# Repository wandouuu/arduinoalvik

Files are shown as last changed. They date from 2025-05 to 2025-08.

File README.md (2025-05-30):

# Autonomy in Action with the Arduino Alvik
Repository of the code used to develop a line following robot with color recognition. Developed by Semih Eski and Brendan Leung, students at Dawson College during the Winter 2025 Semester.
# About This Project
This is an open-source autonomous vehicle project that uses an Arduino Alvik. It extends beyond Alvik's out-of-box capabilities by bringing together a Raspberry Pi 3B+, used for computer vision, and a 3D-printed 5-DOF robotic arm. Alvik leverages a PID algorithm and its infrared sensors to do line following, and its color-recognition sensor to detect colors underneath. A Raspberry Pi and a Pi camera are mounted on a 3D-printed stable makeshift holder that is secured through Alvik's screw threads. When the Alvik detects the color white underneath, it stops and commands, through serial communication, the RPi to run a computer vision program to calculate the distance from Alvik to a ping pong ball placed ahead. The RPi returns the distance to Alvik who accurately calculates time to travel at a fixed RPM, drives and stops next to the ball. The RPi then controls the robotic arm to pick up the ball through the PCA9685 servo board using inverse kinematics. Alvik continues travelling around the track until it detects the color orange, placed next to a basket, in which the robotic arm drops the ping pong ball. Alvik continues moving around the track until it is stopped.
# Features
* PID line following
* HSV color detection
* Touch sensor
* Serial communication
* Computer vision color recognition
* Computer vision distance calculation
* Inverse kinematics
# Hardware Requirements
* Arduino Alvik
* Raspberry Pi 3B+
* 3D printed robotic arm
* PCA9685 servo board
* Raspberry Pi camera module 1
* Jumper wires
* Black electrical tape
* 8xM3x15mm screws
* 6xFS90 micro servos
* 5V/2.5A+ portable power supply
* 5V/5A USB battery pack
# Files
* `serialcomm.py`: Main RPi sketch for serial communication, computer ball recognition and vision distance calculation
* `snap_photo.py`: Captures a photo through the RPi camera
* `distancecalc.py`: RPi sketch for only calculating distance
* `ball_color_detection.py`: RPi sketch for only ball detectiong and drawing a contour
* `line_follower.ino`: Main Arduino sketch for line following, HSV color recognition and serial communication
* `robot_arm_parts`: All the parts to 3D print in .SLDPRT format
# Getting Started
## Wiring Instructions
### Raspberry Pi → Alvik's Nano ESP32: 
* USB-A → USB Micro B
### Raspberry Pi → PCA9685:
* 3.3V → VCC
* SDA → SDA
* SCL → SCL
* GND → GND
### Servos → PCA9685:
* Servo 1 → PCA9685 Pin 0
* Servo 2 → PCA9685 Pin 1
* Servo 3 → PCA9685 Pin 2
* Servo 4 → PCA9685 Pin 3
* Servo 5 → PCA9685 Pin 4
* Servo 6 → PCA9685 Pin 5
## Prerequisites
* Python
* Arduino IDE
* Arduino Alvik Library (should be installed by default)
* Thonny IDE (Raspberry Pi)
* OpenCV (Raspberry Pi)
* NumPy (Raspberry Pi)
* imutils (Raspberry Pi)
## Cloning the repository
```bash
# Navigate on your computer to a directory (folder) in which you contain your repositories
cd directory1/directory2/directory3/.../my_repos

# In your my_repos directory, or whatever your folder name may be, clone our GitHub repository by doing the following
git clone https://github.com/wandouuu/arduinoalvik.git

# Now, you should be in the my_repos folder. From there, go into the arduinoalvik directory to access the content
cd arduinoalvik

# Before installing any dependencies for the Raspberry Pi, ensure that the apt-get function is fully updated
sudo apt-get update

# And install any prerequisites
sudo apt-get install build-essential cmake pkg-config libjpeg-dev libtiff5-dev libjasper-dev libpng-dev libavcodec-dev libavformat-dev libswscale-dev libv4l-dev libxvidcore-dev libx264-dev libfontconfig1-dev libcairo2-dev libgdk-pixbuf2.0-dev libpango1.0-dev libgtk2.0-dev libgtk-3-dev libatlas-base-dev gfortran libhdf5-dev libhdf5-serial-dev libhdf5-103 python3-pyqt5 python3-dev -y

```
## Keeping apt-get updated on the Raspberry Pi
```bash
# Before installing any dependencies for the Raspberry Pi, ensure that the apt-get function is fully updated by writing the following into Raspberry Pi's terminal
sudo apt-get update

# And install any prerequisites
sudo apt-get install build-essential cmake pkg-config libjpeg-dev libtiff5-dev libjasper-dev libpng-dev libavcodec-dev libavformat-dev libswscale-dev libv4l-dev libxvidcore-dev libx264-dev libfontconfig1-dev libcairo2-dev libgdk-pixbuf2.0-dev libpango1.0-dev libgtk2.0-dev libgtk-3-dev libatlas-base-dev gfortran libhdf5-dev libhdf5-serial-dev libhdf5-103 python3-pyqt5 python3-dev -y
```
## OpenCV Installation
```bash
# Still in the Raspberry Pi terminal, type:
pip install opencv-python==4.5.3.56
```

## NumPy Installation
```bash
# Still in the Raspberry Pi terminal, type:
pip install numpy
```

## imutils Installation
```bash
# Still in the Raspberry Pi terminal, type:
pip install imutils
```
Hooray, you have installed now installed the necessary dependencies! You may now get to work!

# How to Use
1. Make a simple, circular track with a white gap at the beginning of a straight segment of track.
2. Attach the wires as indicated in the Wiring Instructions. Note that the camera should be facing the front of the Alvik.
3. Ensure that the Alvik is sufficiently charged.
4. Ensure that the Raspberry Pi is plugged into an outlet or a portable power supply with adequate voltage and amperage.
5. Find the RGB values of the white line, read through Alvik's color-recognition sensor, where the Alvik will stop on the line following track and input them in the `line_follower.ino` if statement with the comparison operators with the rgb_colors list.
6. Upload `serialcomm.py` to the Arduino Alvik using the Arduino IDE.
7. Using `ball_color_detection.py`, ensure that the coloured ping pong ball is detected in your given lighting conditions. Adjust the parameters ORANGE_LOWER and ORANGE_UPPER as needed to detect the ping pong ball.
8. Copy and paste these values across to serialcomm.py.
9. Now, write the directory in `snap_photo.py` of where the calibration photo is stored. 
10. Run the program `snap_photo.py` and disconnect the HDMI cable (ensure the Alvik and the Pi are connected via USB) and run the Alvik by turning it on and pressing the checkmark on the top of it.
11. Once the photo is taken, ensure the calibration photo directory (calib_path variable) is the same as in `serialcomm.py`. 
12. In `serialcomm.py`, write the directory in which the photo of the distance calculation photo will be taken in the capture method of the camera object.
13. Run `serialcomm.py` and detach the HDMI cable, ensuring the Alvik and the Pi are connected via USB.
14. Turn on Alvik and press its checkmark and watch it go!

# Development Notes
- Created as part of the MakerSPACE initiative and Making Things That Matter course at Dawson College.
- Version 1.0.0

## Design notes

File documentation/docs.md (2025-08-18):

# Arduino Alvik: Developing a Project in Engineering Robotics from Scratch!
## Project developed by Semih Eski and Brendan Leung, Report written by Brendan Leung
### Introduction
<p>&nbsp;&nbsp;&nbsp;&nbsp;Independent learning is something that we have struggled with. How do we build a project from scratch? How do we acquire the skills we need to conceive a project we are interested in? Along with our continued interest for computers, programming, computer and mechanical engineering we aimed to learn the art of learning by exploring engineering robotics as beginners and documenting our journey so that future beginners can see how we modeled a path to learning how to develop a project from nothing. We wished to be able to learn on the fly, adapt and conceive a project that involves hardware and software from start to finish. With our project, we were able to get hands-on with robots and software to realize this goal and gain the experience and technical skills we need to create a project from nothing.</p>
<p>&nbsp;&nbsp;&nbsp;&nbsp;Our goal was achieved using the Arduino Alvik robot, a premade robot made by Arduino, an open-source hardware company known for their electronics. Together with this robot, we built a robot capable of picking up coloured ping pong balls from a line following track using a Raspberry Pi, a Linux-based computer used in various electronics projects, to identify the colours of the ping pong balls using a camera. We also designed a custom-made robotic arm for the Alvik, which was integrated with its hardware to help pick up the balls off the ground. </p>

### Project Description
<ul>
<li><b>Objective</b></li>
<p>&nbsp;&nbsp;&nbsp;&nbsp; The goal of our project was to discover a learning path for engineering robotics. We focused on acquiring the experience we needed to develop a project in a field we had and still have a fond interest in, as well as the necessary skills we need to use software and hardware to develop a project. </p>
<li><b>Inspiration</b></li>
<p>&nbsp;&nbsp;&nbsp;&nbsp; When we were young, we became fondly interested in electronics and mechanical devices, but we never knew where to start. We were fascinated at how people were able to make these cool gadgets, but we struggled to put our hands on it. We struggled to program. We struggled to build. But we never struggled to dream that I could program and build things on my own. We knew we had to start somewhere. We knew we had to learn by doing something. So, we chose to design a project with the Arduino Alvik robot, a premade robot conceived by Arduino, an open-source hardware company known for their microcontrollers and other electronics. </p>
<p>&nbsp;&nbsp;&nbsp;&nbsp; While we could have built a robot from scratch, we decided to use the Alvik because it helped us gain a solid foundation for how hardware and software interact with each other without having to think about wiring and connections. For example, we learned along the way that the communication between hardware and software has to be exact. We realized that the way I think the robot would behave with the code we implemented sometimes did not work out in practice. Additionally, we wished to extend the already existing capabilities of the Alvik and learn how different technologies could be implemented with each other. Needless to say, we were ambitious. We used a Raspberry Pi, a Linux-based computer, to help with serial communication between a robotic arm from scratch and the Alvik, so that the Alvik is able to recognize coloured ping pong balls and pick them off the ground using its robotic arm. </p>
<p>&nbsp;&nbsp;&nbsp;&nbsp;Our inspiration largely came from experimenting at the beginning of our project with the robot with my teammate and the project was better understood after learning what we were both capable of.</p>
<li><b>Design and Planning</b></li>
<p>&nbsp;&nbsp;&nbsp;&nbsp; At the beginning of my project, we were not fully sure what to do. We wanted to develop a project using artificial intelligence to make the Alvik drive around autonomously, but soon enough this turned out unfeasible in the time we had. However, we were determined to keep the essence of that idea inside of our project. After much brainstorming, we made our idea much more feasible, incorporating line following features to imitate this autonomous navigation. As described in our journals early on, we began first exploring different functionalities of the robot. Figure 1 below shows us playing around with the robot, attempting to make the Alvik find the object it is closest to.</p>
<figure>
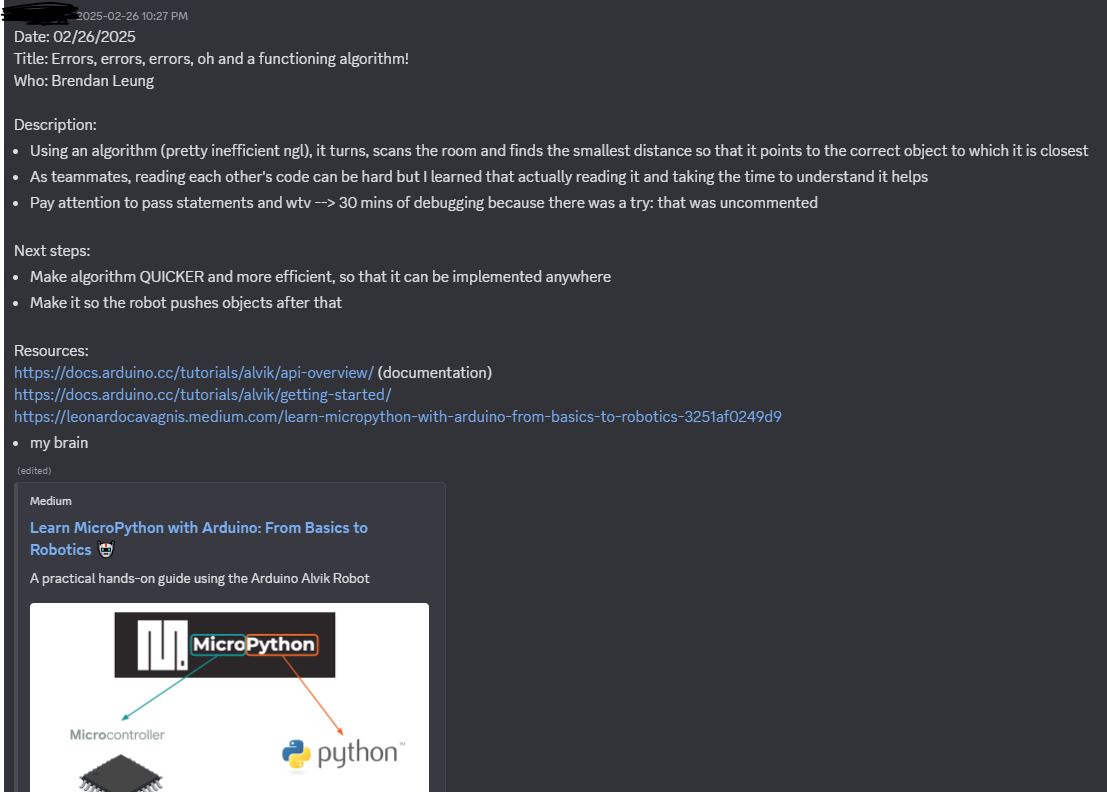
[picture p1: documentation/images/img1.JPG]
Experimenting with Alvik for the First Time!
    
    <figcaption><em>Figure 1. Our history of what we did was written in Discord. In a journal three months ago, we tried making the robot point towards the object it was closest to. It seems like it was successful, but it was quite slow!</em></figcaption>
</figure>
<p>&nbsp;&nbsp;&nbsp;&nbsp;These days helped both of us become familiar with the robot and its capabilities. At the time, we thought of making a robot that could push objects off the table; of course, without making the Alvik fall off the table itself! Because our program was quite straightforward, we wanted to make something more elaborate. </p>
<p>&nbsp;&nbsp;&nbsp;&nbsp;We interviewed a Masters student from the University of Toronto specializing in robotics and AI to help guide us in our project. Our ambition was soon met with realistic expectations, as she told us that AI would be quite difficult and we should only implement it if we had time. Then, she told us that we should divide our project into little chunks, tackling each small problem progressively and combining them together later. This strategy helped me in the project development because, as beginners, we were quite overwhelmed with the amount of features we had to consider. Instead, breaking the project up into smaller, more manageable pieces made the project seem more achievable. This is how we tackled different parts of the project. </p>
<p>&nbsp;&nbsp;&nbsp;&nbsp;This idea had major implications on how we worked on our project because we knew we had a learning path. We had a roadmap. We knew we wanted to make a robot capable of driving itself around and have some image recognition capabilities. With that, in the months following, we focused on developing Alvik’s functions: line following, object detection, colour detection and etc. Semih also focused on creating the robotic arm and integrating it with our robot. Below is a snapshot of the prototype of the Alvik along with its robotic arm.<p>
<figure>
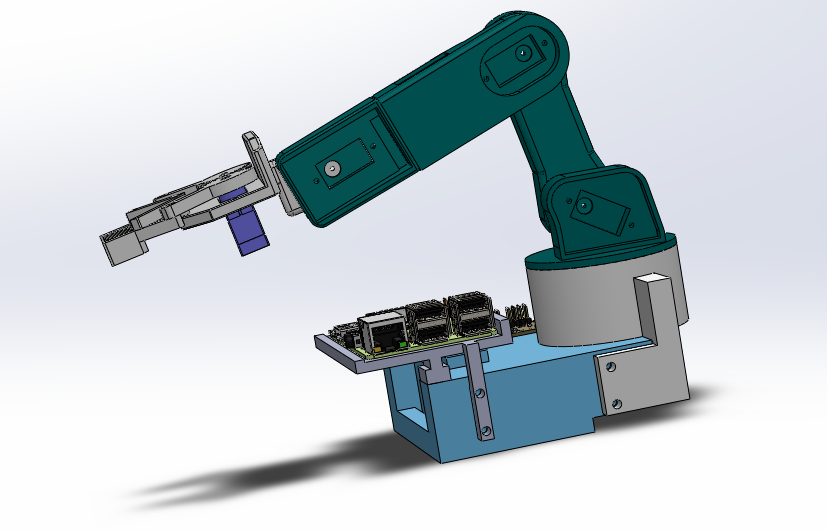
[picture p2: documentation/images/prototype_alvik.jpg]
Prototype of Alvik and its Robotic Arm
  
  <figcaption><em>Figure 2. The Alvik is shown with a Raspberry Pi holder near the front of the Alvik while a robotic arm sits as a counterbalance towards the back of the Alvik.</em></figcaption>
</figure>
<p>&nbsp;&nbsp;&nbsp;&nbsp; In our final stage, we implemented all these smaller chunks together in what will be a robot which is capable of line following and picking up coloured ping pong balls in its vicinity.</p>
</ul>

### Implementation
<ul>
<li><b>Hardware Setup</b></li>
<ul>
<li>Components Used</li>
<ul>
<li>Arduino Alvik</li>
<li>Raspberry Pi 3 Model B+</li>
<li>Raspberry Pi Camera Module 1</li>
<li>3D Printed Robotic Arm</li>
<li>Six SG90 Positional Servos</li>
<li>PCA9685 Servo Driver</li>
<li>Power Supplies</li>
</ul>
<li>Hardware Schematics</li>
<p>&nbsp;&nbsp;&nbsp;&nbsp; The serial connection between the Arduino Alvik and the Raspberry Pi is made via Universal Serial Bus (USB). The Alvik should be connected to the Raspberry Pi using its USB-C port, connected to the designated USB-A port on the Raspberry Pi, as shown in the diagram below. Note that if a different port is chosen, the USB port chosen to establish serial communication in the Python code will have to be changed.</p>

<figure>
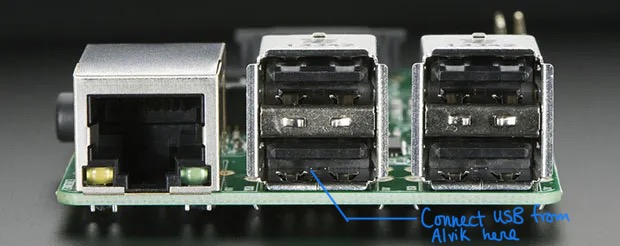
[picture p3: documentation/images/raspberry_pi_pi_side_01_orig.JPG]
Side image of the USB-A connection on the Raspberry Pi
    
    <figcaption><em>Figure 3. Connect the Alvik to the Raspberry Pi in the exact port on the Raspberry Pi as shown. The other end should be connected to the USB-C port of the Alvik.</em></figcaption>
</figure>

<p>&nbsp;&nbsp;&nbsp;&nbsp; To connect the servos, connect the female-to-female jumper wires between the Raspberry Pi and the Servo Driver as follows. Also, attach the Raspberry Pi Camera Module in the slot that is named "Camera". This is shown in the figure below:</p>
<figure>
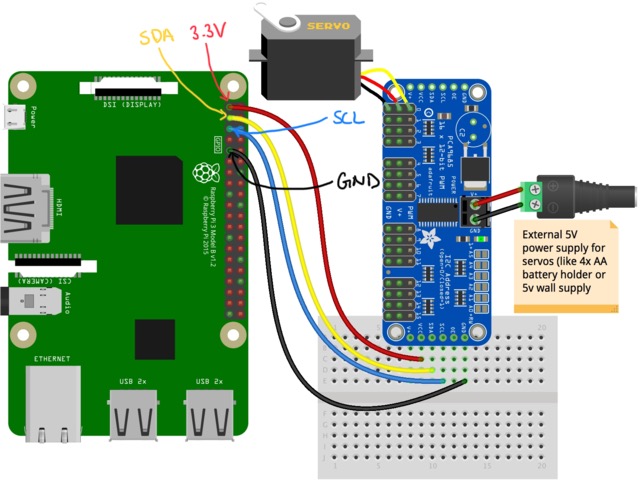
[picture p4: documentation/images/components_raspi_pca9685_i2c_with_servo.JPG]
Connections on the Raspberry Pi and between it and the Servo Drivers
    
    <figcaption><em>Figure 4. Connect the female-to-female wires as shown between the Raspberry Pi and the Servo Driver. Furthermore, connect the Raspberry Pi Camera Module in the "Camera" slot.</em></figcaption>
</figure>
<p>&nbsp;&nbsp;&nbsp;&nbsp; Note that to read any information that is serially monitored by the Alvik or the Raspberry Pi, the Raspberry Pi (not the Alvik) must be connected to a monitor via HDMI. This is because the Alvik sends all its serial information to the Raspberry Pi, and the Raspberry Pi can display this information along with its own. Finally, the Raspberry Pi must be plugged into an outlet, while the Alvik can be charged. Ensure as well that the wiring has enough slack to allow for the Alvik to be mobile.</p>
</ul>

<li><b>Software Development</b></li>
<ul>
<li>Libraries Used</li>
<ul>
<li>Arduino Alvik Library</li>
<li>Serial Library</li>
<li>OpenCV</li>
<li>OS</li>
<li>NumPy</li>
<li>imutils</li>
</ul>
</ul>
<p>&nbsp;&nbsp;&nbsp;&nbsp; The code specific to the Alvik was developed using the Arduino IDE, while the code for the Raspberry Pi was written on the Pi's text editor. All of Alvik's functions can be found on <a href = "https://docs.arduino.cc/tutorials/alvik/api-overview/">Alvik's API</a>, which provides all the details of each method. It is important to note that while Arduino claims that all functions work between MicroPython and C++, we encountered runtime errors where the C++ compiler was unable to locate a function like alvik.drive(). We used Alvik's API extensively in our project, making this a valuable site for learning how to make the Alvik move, how to use its sensors, etc. We also used Arduino's own courses, found <a href = "https://www.arduino.cc/education/courses">here</a>, which helped us learn early on how to make Alvik follow a line and detect objects in front of it. It is a fantastic way to familiarize yourself with all that Alvik offers out-of-the-box before trying out more ambitious ideas. </p>
<p>&nbsp;&nbsp;&nbsp;&nbsp; To detect the ping pong balls, we used OpenCV, a library used for real-time computer vision, which runs locally on the Raspberry Pi and then sends the information back to the Alvik using serial communication. The code below, inspired by <a href="https://github.com/freedomwebtech/colortracking/blob/main/test.py">this GitHub repository</a>, allows us to identify orange coloured ping pong balls. We initially wished to deploy a machine learning model to identify our ping pong balls; however, it was hard to deploy because of compatibility issues between Windows and Raspberry Pi. So, we elected to detect colours instead because it was compatible and, more importantly, lightweight to run on the Raspberry Pi. Still, OpenCV provides us with a powerful computer vision library that suits our needs. NumPy was used extensively to store HSV values, while OS provided us with an easier way to manage file directories.</p>

```py
# Import OpenCV and NumPy Libraries
import cv2
import numpy as np

# Initialize camera
cap = cv2.VideoCapture(0)
cap.set(cv2.CAP_PROP_FRAME_WIDTH,  640)
cap.set(cv2.CAP_PROP_FRAME_HEIGHT, 480)

# Upper and Lower Bounds for the color to be identified (in HSV NOT RGB)
ORANGE_LOWER = np.array([ 6, 120, 160]) # Set these values depending on your specific lighting conditions and what color you would like to identify
ORANGE_UPPER = np.array([26, 255, 255])

kernel = np.ones((5, 5), np.uint8)   # this is used for morphology

while True:
    success, frame = cap.read()

    # If fails to read camera data
    if not success:
        print("Camera read failed — exiting.")
        break

    # Color spectrum used
    hsv = cv2.cvtColor(frame, cv2.COLOR_BGR2HSV)

    # Color mask
    orange_mask = cv2.inRange(hsv, ORANGE_LOWER, ORANGE_UPPER)
    mask = orange_mask

    mask = cv2.morphologyEx(mask, cv2.MORPH_OPEN,  kernel, iterations=1)
    mask = cv2.morphologyEx(mask, cv2.MORPH_CLOSE, kernel, iterations=1)

    contours, _ = cv2.findContours(mask, cv2.RETR_EXTERNAL, cv2.CHAIN_APPROX_SIMPLE)
    
    # If it detects an orange mask
    if contours:
        c = max(contours, key=cv2.contourArea)
        if cv2.contourArea(c) > 300:        # Ensures that tiny specs are not identified
            
            # Locates the position of the color to be identified
            (x, y), radius = cv2.minEnclosingCircle(c)
            centre = (int(x), int(y)); radius = int(radius)

            cv2.circle(frame, centre, radius, (0, 255,   0), 2)
            cv2.circle(frame, centre,   3,    (0,   0, 255), -1)
            cv2.putText(frame, "orange ball",
                        (centre[0] - 40, centre[1] - radius - 10),
                        cv2.FONT_HERSHEY_SIMPLEX, 0.6, (255, 255, 255), 2)

    cv2.imshow("Mask (debug)", mask)
    cv2.imshow("Ball contour", frame)

    if cv2.waitKey(1) & 0xFF == ord('q'):
        break

cap.release()
cv2.destroyAllWindows()
```
<p>&nbsp;&nbsp;&nbsp;&nbsp; The success rate of this piece of software heavily depends on the lighting conditions in which we were in. We struggled mostly to land consistent results, given that the lighting conditions in which we found ourselves when testing our software were always different. We always had to constantly tweak the lower and upper bounds for colour so that the orange ball is detected in each specific lighting conditions in which we were in. Not only did the orange ball have to be detected, but it also had to enclose the orange ball entirely and accurately pinpoint its center. This is because this was used to calculate the distance between the Alvik and the ping pong in front of it, using the code below, which was developed with the help of <a href = "https://pyimagesearch.com/2015/01/19/find-distance-camera-objectmarker-using-python-opencv/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">this website</a>. Your image should look like this: </p>

<figure>
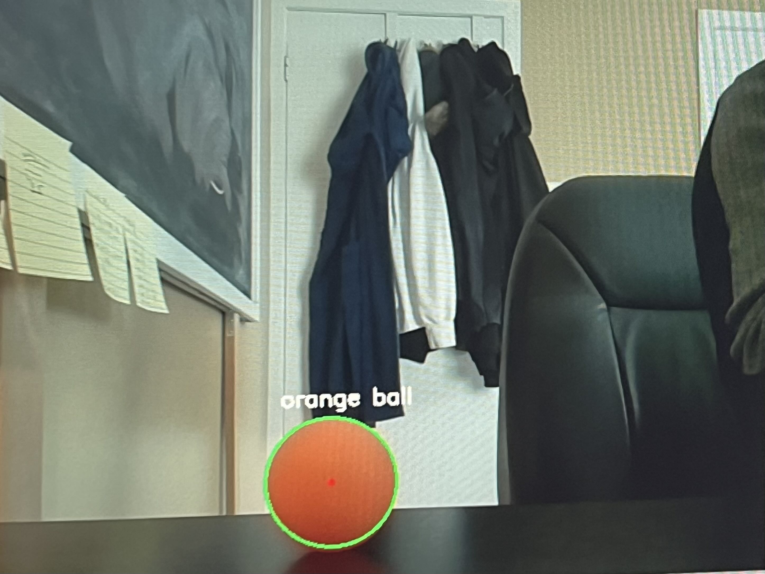
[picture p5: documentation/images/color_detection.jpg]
Orange Ping Pong Ball Perfectly Enclosed by Colour Detection Algorithm
    
    <figcaption><em>Figure 5. The colour you wish to detect should be perfectly enclosed like the photo shown above, with the red dot at the center.</em></figcaption>
</figure>

```py
# Import the necessary packages
from imutils import paths
import numpy as np
import imutils
import cv2
import os

KERNEL = np.ones((5, 5), np.uint8)       

# These bounds are exactly like the code for the ball color detection alone
ORANGE_LOWER = np.array([4,140,58])
ORANGE_UPPER = np.array([12,214,129])     

# This takes the code from the ball color detection in order to create a circle around the ping pong ball
def find_marker(image):
    hsv = cv2.cvtColor(image, cv2.COLOR_BGR2HSV)
    mask = cv2.inRange(hsv, ORANGE_LOWER, ORANGE_UPPER)

    mask = cv2.morphologyEx(mask, cv2.MORPH_OPEN, KERNEL, iterations=1)
    mask = cv2.morphologyEx(mask, cv2.MORPH_CLOSE, KERNEL, iterations=1)

    cnts = cv2.findContours(mask, cv2.RETR_EXTERNAL, cv2.CHAIN_APPROX_SIMPLE)
    cnts = imutils.grab_contours(cnts)
    if not cnts:
        return None
    c = max(cnts, key=cv2.contourArea)
    if cv2.contourArea(c) < 200:
        return None
    (x, y), radius = cv2.minEnclosingCircle(c)
    return (x, y), radius

# Calculates the distance from camera
def distance_to_camera(knownWidth_cm, focalLength_px, perWidth_px):
    return (knownWidth_cm * focalLength_px) / perWidth_px

# Below, insert the path to the photo that is required to calibrate the distance calculations
calib_path = "path of calibration photo goes here"

# Need to put the known distance of the ping pong ball from the camera from the calibration photo
KNOWN_DISTANCE_CM = 33.50 # Distance of object from camera
KNOWN_WIDTH_CM    = 4.0 # Width of object 

# Raises an error if no calibration photo exists
if not os.path.isfile(calib_path):
    raise FileNotFoundError(f"calibration image missing")

# Reads the image
calib_image = cv2.imread(calib_path)
# Before taking the photo, ensure that the camera actually detects and puts a perfect circle around the ping pong ball
res = find_marker(calib_image)
# Raises an error if the ball detection software does not detect the ball. This is why you must ensure the ball is detected prior to taking the photo.
if res is None:
    raise RuntimeError("No ball found")
(center0, radius0) = res
perWidth0 = 2 * radius0 
focalLength_px = (perWidth0 * KNOWN_DISTANCE_CM) / KNOWN_WIDTH_CM

cv2.namedWindow("image", cv2.WINDOW_NORMAL)
cv2.resizeWindow("image", 800, 600)

# Code checks for photos in a certain directory of which you have stored photos of distances of ping pong balls you wish to calculate
for imagePath in sorted(paths.list_images("path of photo goes here")): # Once there is a calibration photo, indicate where your photos are taken
    # Path of image
    image = cv2.imread(imagePath)

    # Finds ball in image
    res = find_marker(image)

    # If no ball is found, nothing is returned
    if res is None:
        dist_cm = None
    else: # Otherwise, it calculates the position and distance of the ball from the image itself
        (x, y), radius = res
        perWidth = 2 * radius
        # Calculates the distance from the camera
        dist_cm = distance_to_camera(KNOWN_WIDTH_CM, focalLength_px, perWidth)

        center = (int(x), int(y))
        cv2.circle(image, center, int(radius), (0, 255, 0), 2)
        cv2.circle(image, center, 3, (0, 0, 255), -1)

    # Displays the distance if the photo has a ping pong ball detected
    if dist_cm is not None:
        cv2.putText(
            image,
            f"{dist_cm:.1f} cm",
            (10, image.shape[0] - 10),
            cv2.FONT_HERSHEY_SIMPLEX,
            1.0,
            (0, 255, 0),
            2
        )
    # Displays image
    cv2.imshow("image", image)
    key = cv2.waitKey(0) & 0xFF
    if key == ord('q'):
        break

cv2.destroyAllWindows()
```
<p>&nbsp;&nbsp;&nbsp;&nbsp; With this strategy, a major downside we encountered is that we needed to take a calibration photo every time the ping pong balls found themselves in new lighting situations, since the colours were always different. Had we used an image detection model, this would not be necessary. Also, we had to always ensure that the whole ping pong ball was enclosed by the model. Otherwise, it would deliver inaccurate results. This was a major milestone in our project because this was required to tell the Alvik how far the ping pong ball is positioned and enable it to travel that distance. For that, we used serial communication between the Alvik and the Raspberry Pi. </p>
<p>&nbsp;&nbsp;&nbsp;&nbsp; We found that establishing serial communication via Universal Serial Bus (USB) between the Alvik and the Raspberry Pi was quite straightforward.  We used C++ because of its serial capabilities, which we were not able to deploy with MicroPython on Alvik's end. Obviously, both the Alvik and Raspberry Pi must be connected via USB to communicate with each other. Here is the code from Alvik's end: </p>

```ino
// Contains Serial features
#include "Arduino_Alvik.h"
Arduino_Alvik alvik;
String readString;

void setup() {
  // In the setup, it is important to initialize Serial to receive and send serial messages
  Serial.begin(115200);
  while(!Serial){
    ; // wait for USB serial to come out
  }
  alvik.begin();
  alvik.left_led.set_color(0,0,1);
  alvik.right_led.set_color(0,0,1);

  while(!alvik.get_touch_ok()){
    delay(50);
  }
}

void loop() {
  while (!alvik.get_touch_cancel()){

    alvik.set_illuminator(false); // turns off the illuminator below the Alvik for the duration of the program
    alvik.get_line_sensors(line_sensors[0], line_sensors[1], line_sensors[2]); // returns IR data to the list line_sensors
    alvik.get_color_raw(rgb_colors[0],rgb_colors[1],rgb_colors[2]); // returns RGB values into the list rgb_colors
    error = calculate_center(line_sensors[0], line_sensors[1], line_sensors[2]); // calculates deviation from the line
    control = error * kp; # the amount of adjustment Alvik needs to stay on course (on the line)
    // For Serial Monitoring: prints the RGB colours the Alvik sees with its colours sensors
    Serial.print(rgb_colors[0]);
    Serial.print("\t");
    Serial.print(rgb_colors[1]);
    Serial.print("\t");
    Serial.print(rgb_colors[2]);
    Serial.print("\n");

    // Once the Alvik detects a white gap in the line, it stops to check for the ping pong ball around it
    if ((rgb_colors[0] == 5 || rgb_colors[0] == 4) && (rgb_colors[1] == 4) && (rgb_colors[2] == 4)){ // If the triple (R,G,B) is any of these values, strong indication that white is below the Alvik (depends on the white)
      // Alvik moves forward to a position where it will not redetect the white line a second time
      alvik.left_led.set_color(1,0,0); 
      alvik.right_led.set_color(1,0,0);
      alvik.brake();
      delay(2000);
      alvik.rotate(12);
      delay(2000);
      alvik.set_wheels_speed(10,10);
      delay(2000);
      alvik.brake();
      delay(3000);

      // Alvik sends a message to Pi through Serial
      Serial.println("photo");

      // While the Alvik does not receive any bytes, it remains at a standstill
      while(Serial.available() <= 0){
        alvik.brake();
      } 
      // Once there is bytes flowing, the Alvik decodes the bytes which are characters and concatenates them into a string for the full message
      while(Serial.available()){
        delay(3);
        if (Serial.available() > 0 ){
          char c = Serial.read();
          readString += c;
        }
      }

      // Using the information that Alvik has received from the Pi, it calculates the speed it needs to reach the object in five seconds
      int distance = readString.toInt(); // mm
      int rpm = 10; // rpm
      int time = 60000*distance/(rpm*3.14159*3.4); // milliseconds
      Serial.println(time); // prints the time needed in milliseconds in Serial Monitor
      alvik.set_wheels_speed(rpm,rpm); // Wheel speed set for Alvik to approach object
      delay(time); // Delays the exact time needed to travel the distance required
      alvik.brake(); // Alvik stops for 3 seconds to show it has ended this operation
      delay(3000);

    }

    // Lights to indicate what the Alvik is doing (turning, straight, etc.)
    if (control > 0.2){
      alvik.left_led.set_color(1,0,0);
      alvik.right_led.set_color(0,0,0);
    }
    else{
      if (control < -0.2){
        alvik.left_led.set_color(0,0,0);
        alvik.right_led.set_color(1,0,0);
      }
      else{
        alvik.left_led.set_color(0,1,0);
        alvik.right_led.set_color(0,1,0);
      }
    }

    alvik.set_wheels_speed(30-control, 30+control);
    delay(100);
  }
  
  while (!alvik.get_touch_ok()){
    alvik.left_led.set_color(0,0,1);
    alvik.right_led.set_color(0,0,1);
    alvik.brake();
    delay(100);
  }
}

// Line following calculating the error from the line itself
float calculate_center(const int left, const int center, const int right){
  float centroid = 0.0; 
  float sum_weight = left + center + right;
  float sum_values = left + center * 2 + right * 3;
  if (sum_weight!=0.0){                                                         // divide by zero protection
    centroid=sum_values/sum_weight;
    centroid=-centroid+2.0;                                                     // so it is right on robot axis Y
  }
  return centroid;
}
```

<p>With just a few lines of code, we were able to send and receive messages between the Alvik and the Raspberry Pi. We used <a href="https://forum.arduino.cc/t/read-line-from-serial/98251">this forum post</a> to help us read entire lines of messages from the Pi, while this <a href = "https://protonestiot.medium.com/communication-between-esp32-and-raspberry-pi-using-uart-7b776786c08a">fantastic post from Protonest IoT</a> provided us with the explanations and code required to communicate between the Pi and the Alvik. Also, since we must take a new photo every time the Alvik was at the line, this <a href = "https://www.youtube.com/watch?v=nx8gDSS1vO4">video</a> helped us program the process of taking a picture with the Pi Camera and storing it in a file on the Raspberry Pi. Below is the code from the Pi's end, which we have combined with the distance calculation software. Refer to the above code snippets for more details on the distance calculation segments of the code.</p>

```py

## Libraries for taking photos and serial communication on Pi's end
import serial, time
from picamera import PiCamera
import time
import math

# Necessary packages for distance calculations
from imutils import paths
import numpy as np
import imutils
import cv2
import os

# See previous code snippets for details
KERNEL = np.ones((5, 5), np.uint8)       
ORANGE_LOWER = np.array([4,140,58])
ORANGE_UPPER = np.array([12,214,129])

# Establish Serial Communication from the USB port
ser = serial.Serial('/dev/ttyACM0', 115200, timeout=1)
time.sleep(2)

# Create a camera instance of PiCamera() to take photos
camera = PiCamera()

# See previous code snippets for details
def find_marker(image):
    hsv = cv2.cvtColor(image, cv2.COLOR_BGR2HSV)
    mask = cv2.inRange(hsv, ORANGE_LOWER, ORANGE_UPPER)

    mask = cv2.morphologyEx(mask, cv2.MORPH_OPEN, KERNEL, iterations=1)
    mask = cv2.morphologyEx(mask, cv2.MORPH_CLOSE, KERNEL, iterations=1)

    cnts = cv2.findContours(mask, cv2.RETR_EXTERNAL, cv2.CHAIN_APPROX_SIMPLE)
    cnts = imutils.grab_contours(cnts)
    if not cnts:
        return None
    c = max(cnts, key=cv2.contourArea)
    if cv2.contourArea(c) < 200:
        return None
    (x, y), radius = cv2.minEnclosingCircle(c)
    return (x, y), radius

# See previous code snippets for details
def distance_to_camera(knownWidth_cm, focalLength_px, perWidth_px):
    return (knownWidth_cm * focalLength_px) / perWidth_px

# See Previous code snippets for details
KNOWN_DISTANCE_CM = 18.25
KNOWN_WIDTH_CM = 4

# See Previous code snippets for details
calib_path = "insert calibration photo path here"
if not os.path.isfile(calib_path):
    raise FileNotFoundError(f"calibration image missing")

# See Previous code snippets for details
calib_image = cv2.imread(calib_path)
res = find_marker(calib_image)
if res is None:
    raise RuntimeError("No ball found")
(center0, radius0) = res
perWidth0 = 2 * radius0 
focalLength_px = (perWidth0 * KNOWN_DISTANCE_CM) / KNOWN_WIDTH_CM

while True:
  # While on loop, the Pi reads its serial input for any bytes (messages)
	line = ser.readline().decode('utf-8').strip()

  # If the line from the Alvik writes "photo" (see Alvik's Serial communication end)
	if line == "photo":
		time.sleep(2) # Wait 2 seconds

    # Take a photo named dist.jpg in some file directory
		camera.capture("/home/mydir/images/dist.jpg")

    # For every image in the images directory
		for imagePath in sorted(paths.list_images("/home/mydir/images")):
			# Image is read
      image = cv2.imread(imagePath)
      # Find the ping pong ball in image
			res = find_marker(image)

    # If there is no ping pong ball in image, nothing is sent
		if res is None:
      # Encodes message that the distance travelled should be zero, because no object was found
			dist_cm = 0
      print("No ball found.")
      message = f"{str(math.floor(dist_cm))}"
      encoded_message = message.encode()
      ser.write(encoded_message)

    # If there is a ping pong ball in image
		else:
      (x, y), radius = res
      perWidth = 2 * radius
      # Calculates the ping pong ball's distance to the Pi Camera (Alvik)
      dist_cm = distance_to_camera(KNOWN_WIDTH_CM, focalLength_px, perWidth)
      # Message is prepared
      message = f"{str(math.floor(dist_cm))}"
      # The message must be encoded into bytes for transmission
      encoded_message = message.encode()
      # Pi writes to Alvik the message with the distance which the Alvik will use for its calculations
      ser.write(encoded_message)
		time.sleep(5)
		break
		
```
<p>&nbsp;&nbsp;&nbsp;&nbsp; At this point in the development of all our software components, it was extremely cool seeing all of our various features that we wished to implement come together and work together the way they did. We began seeing results from breaking our project into smaller parts which we then combined together here, of which we are extremely proud. We will leave with a snippet of us testing out our Serial communication and distance calculations using this unconventional setup!</p>

<figure>
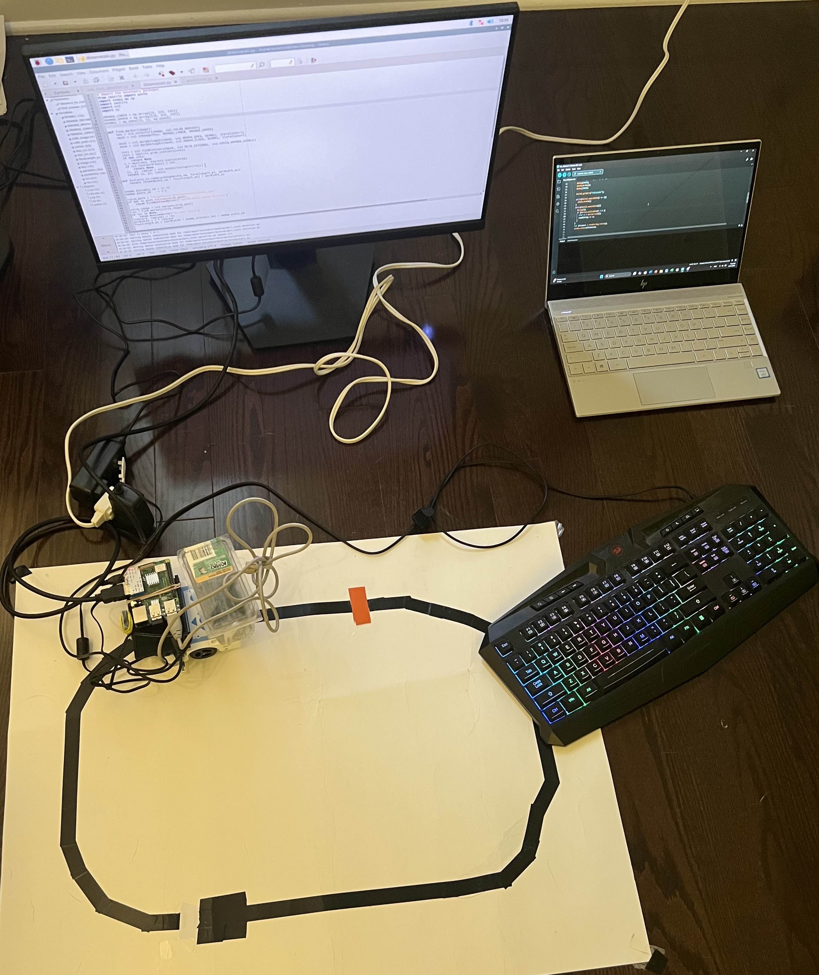
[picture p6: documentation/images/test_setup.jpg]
Test Setup During Software Development
    
    <figcaption><em>Figure 6. Lots of wires needed when we tested serial communication and distance calculation together!</em></figcaption>
</figure>

<li><b>Sensor Documentation</b></li>
<p>&nbsp;&nbsp;&nbsp;&nbsp; During the development of my project, we used tried out certain functions of sensors that were not used in the final product. Nevertheless, we will document their functions and present sample code for their uses.  The most notable sensor we have used extensively but its role in my project was reduced is the time of flight (ToF) sensor. The infrared (IR) sensors and the colour sensors, meanwhile, are used in every part of my project. We will begin with the time of flight sensor. </p>

<ul>
<li>Time of Flight Sensor</li>
<p>&nbsp;&nbsp;&nbsp;&nbsp; The purpose of the ToF sensor is to calculate the distance between the Alvik and its surrounding environment. It achieves this by calculating the time it takes for light to travel from the Alvik and back. Knowing the speed of light and the time it takes to travel back to the Alvik, it is able to calculate the distance between objects. This is similar to using an ultrasonic sensor to measure distance, only that the sensor emits light instead of ultrasonic frequencies. Now, the Alvik is able to calculate the distance objects directly in front of it up to objects forty-five degrees to its left or right. Furthermore, the Alvik can detect objects around forty-five degrees below or above it as well. We encountered trouble during our project using the Alvik's ToF sensors, where it would start hallucinating objects in front of it and stopping despite objects not present in front of it. This forced us to abandon using the sensor altogether due to its inconsistency. </p>
<p>&nbsp;&nbsp;&nbsp;&nbsp;We shall only show code for the ToF sensor in MicroPython, although we have since migrated to C++ for the purposes of Serial Communication. As shown below, the get_distance() function returns the distance as a 5-tuple, one for each direction: the left, the center left, the center, the center right and the right.  </p>

```py
# The get_distance function returns the distance for five different angles in front of the Alvik. Note that it returns values in centimeters.
left, cleft, center, cright, right = alvik.get_distance()

```

<p>&nbsp;&nbsp;&nbsp;&nbsp; Combined with a while loop and if statements, we combined these functions so that the Alvik can line follow while always being aware of its surroundings. Unfortunately, because the Alvik hallucinated invisible objects constantly, we had to remove this feature entirely from our project. However, below was the code we used that combined line following and letting Alvik go around objects that it may encounter in its path.</p>

```py
while True:
  left, cleft, center, cright, right = alvik.get_distance()
  try:
    # If the object is directly in front of the Alvik
    if center <= 12.5:
      alvik.brake() # Stops
      delay(200)
      alvik.rotate(90,unit="deg") # Turns 90 counterclockwise degrees
      delay(200)
      alvik.set_wheels_speed(9,9) # Moves forward for a bit
      delay(2000)
      alvik.rotate(-90,unit="deg") # Turns back 90 degrees clockwise to see if object is still there
      delay(200)

    # If the object is not directly in front of Alvik, but slightly towards its right (Usually triggered around corners)
    elif cright <= 14 and cright < center:
      alvik.brake()
      delay(200)
      alvik.rotate(60,unit="deg") # Turns 60 degrees counterclockwise
      delay(200)
      alvik.set_wheels_speed(9,9) # Moves forward for a bit
      delay(2000)
      alvik.rotate(-90,unit="deg") # Turns back 90 degrees clockwise to see if object is still there
      delay(200)
    # If the object is truly towards the very right of the Alvik
    elif right <= 9.5 and right < center and right < cright:
      alvik.brake()
      delay(200)
      alvik.rotate(30,unit="deg") # Turns 30 degrees counterclockwise
      delay(200)
      alvik.set_wheels_speed(9,9) # Moves forward for a bit
      delay(5000)
      alvik.rotate(-60,unit="deg") # Turns back 60 degrees clockwise to see if object is still there  
      delay(200)
    
    # Otherwise, continue updating error relative to the line and line following
    else:
      error = get_position_error()
      integral += error
      derivative = error - last_error
  
      # PID calculation to determine speed adjustment
      adjustment = KP * error + KI * integral + KD * derivative
```
<li>Colour Sensor</li>
<p>&nbsp;&nbsp;&nbsp;&nbsp; The Alvik also has a colour sensor on the bottom of the Alvik which helps identify colours on various surfaces. The Alvik can detect colours using Red Green Blue (RGB) or Hue, saturation and value (HSV) spectrums. For the purposes of our project, we use the Alvik's colours sensors to help the Alvik know when to stop and look at its surroundings for the ping pong balls it is trying to pick up. We first struggled with this sensor because either the room we conducted colour sensing on was dark or too bright, which hindered the accuracy of the colours sensed by the Alvik. It turns out it is quite unreliable because we had to change the integer RGB values each time we were in a new lighting situation by reading through the Serial monitor, but we managed to get it to work. The Alvik can also label colours, but we found this to be much more unreliable than using explicit values for RGB, since the readings are not as precise as with exact values that the sensors record. Shown below is a code snippet of how to use the colour sensors to detect a yellow line. By incorporating the get_color_raw() method in a while loop, which we have omitted for space, we are able to obtain the colours readings at any time. Note that we had to identify the RGB values of the yellow tape using the Serial Monitor prior to program our Alvik. </p>

```ino
// List containing colors of RGB
int rgb_colors[3];

alvik.get_color_raw(rgb_colors[0],rgb_colors[1],rgb_colors[2]); // returns RGB values into the list rgb_colors

// It is best to print out the values of the colors to determine what color you want to stop at
Serial.print(rgb_colors[0]);
Serial.print("\t");
Serial.print(rgb_colors[1]);
Serial.print("\t");
Serial.print(rgb_colors[2]);
Serial.print("\n");

// This compares the values of the returned RGB colors in the rgb_colors list against the desired triples (R,G,B) you wish for this code to run if the condition is true
if ((rgb_colors[0] == 6 || rgb_colors[0] == 5) && (rgb_colors[1] == 5) && (rgb_colors[2] == 5 || rgb_colors[2] == 4)){ 
      alvik.left_led.set_color(1,0,0); // brake lights
      alvik.right_led.set_color(1,0,0);
      alvik.brake();
      delay(2000);
    }
```

<li>Infrared Sensors</li>
<p>&nbsp;&nbsp;&nbsp;&nbsp; The infrared sensors found on the bottom of the Alvik are an important piece for line following. These sensors work by emitting infrared light onto the ground and photoreceptors detect the amount of reflected light. The lower the reflected light, the darker it is, indicating the presence of a line. Conversely, the more reflected light there is, it strongly suggests the surface is white, since white light reflects light, whereas a black surface absorbs. We originally implemented our line following solution using the IR sensors in MicroPython, so we will provide a code snippet with that language. For line following, we use Proportional Integral Derivative, a line following technique that attempts to minimize three factors: the cross track error, the cross track error rate and the lane offset. By minimizing these three factors, the Alvik is able to follow a line precisely and accurately. This <a href="https://www.youtube.com/watch?v=4Y7zG48uHRo&ab_channel=AerospaceControlsLab">video</a> provides a solid explanation on how PID works. </p>
<p>&nbsp;&nbsp;&nbsp;&nbsp; In the code snippet below, we provide a function which calculates the deviation of the Alvik from the line below it using the data gathered from the IR sensors, retrieved using the get_line_sensors() method.</p>

```py
# Function to determine positional error from the line
def get_position_error():
  # The IR sensors have three positions on the Alvik, all facing downwards. There is one towards the left, one towards the right and one in the center
  ir_left, ir_center, ir_right = alvik.get_line_sensors()
  total = ir_left + ir_center + ir_right
  # Formula to calculate the error between the Alvik's orientiation vs. the line
  error = ((ir_left * 1 + ir_center * 2 + ir_right * 3) / total) - 2
  return error

```

<p>&nbsp;&nbsp;&nbsp;&nbsp; When incorporated in a while loop, we are able to know how much the Alvik is deviating from the line at any moment in time. This allows us to correct and adjust the Alvik to stay on course.</p>

```py
while True:
  try:
    # The Alvik gets the error at any time
    error = get_position_error()
    integral += error
    derivative = error - last_error

    # PID calculation to determine speed adjustment
    adjustment = KP * error + KI * integral + KD * derivative

    # Adjusts speeds
    left_speed = BASE_SPEED + adjustment
    right_speed = BASE_SPEED - adjustment

    # Ensure speed stay in range 0-70RPM
    left_speed = max(0, min(70, left_speed))
    right_speed = max(0, min(70, right_speed))
    
    # The Alvik follows the line at these exact speeds that keep it line following
    alvik.set_wheels_speed(left_speed, right_speed)
    last_error = error
    sleep(0.1)

  except KeyboardInterrupt as e:
    print('over')
    alvik.stop()
    sys.exit()
```

</ul>
<p>&nbsp;&nbsp;&nbsp;&nbsp; Overall, the sensors that are equipped on the Alvik are quite good. We encountered many issues, however, with the time of flight sensor, forcing us to not use it. When we followed the Alvik around and recorded the readings on the distances, we found that the Alvik would jump from objects that were hundreds of centimeters away to a mere ten centimeters away. This unpredictable behaviour was unfortunately something we could not fix. Had we had more time, we would have attached an external, more reliable sensor for our needs. We would also like to note that we struggled to implement the colour sensor, since its readings were not consistent as well. We found that surrounding light, the warmth of the light and the light under the Alvik can negatively affect the Alvik's ability to identify and record accurate values for the colours below it. As a result, we suggest to use Alvik's colour sensors only when the colour that is trying to be detected is distinct and unique (e.g. yellow, neon green). We also think constant lighting will greatly help as well to produce consistent results. </p>
</ul>

### Results
<p>&nbsp;&nbsp;&nbsp;&nbsp; We were able to implement line following, colour recognition and serial communication features on the Arduino Alvik. Along the development of the robot, we were unable to implement object detection into the Alvik since the Time of Flight sensor delivered unpredictable and inconsistent readings. Regardless, our final Alvik runs wired, allowing the Alvik and the Pi to communicate between each other and identify the location of the ping pong ball on a designated area of our track that the Alvik stops at. It is able to then move forward exactly to the position of the ping pong ball and stop there.

### Analysis / Lessons Learned
<p>&nbsp;&nbsp;&nbsp;&nbsp; We came out of this project with a better understanding of how to construct a learning path towards our end goal, which was to acquire experience on integrating hardware and software together. We were able to coordinate our roles well, which helped us reach this late stage in our project's development. We communicated our ideas effectively between each other: by documenting what we did on Discord so that each of us could know what had been done, by drawing images that help us visually understand what we are trying to achieve and more. Looking back, we could have better documented our code with comments because when one of us had the robot and new updates to the code were added, we would not understand it at first. We have now also acquired the experience and skills needed to make a project of this scale, whether they are technical, research or communication skills. Prior to getting the Alvik, we had limited knowledge about robotics, let alone hardware and software, but now we have a clearer understanding of how to learn how to integrate hardware and software together, along with debugging skills from all the problems we encountered, whether it was the ToF sensor, the colour detection sensor or how to even test our Alvik while we have yet to implement its batteries. We combined ideas from resources online and from our own brainstorming and adjusted each feature to our liking, resulting with an Alvik that has its feature set extended beyond its out-of-the-box features. </p>

### Discussion and Conclusion
<p>&nbsp;&nbsp;&nbsp;&nbsp; Looking back at how the project came to be, we have realized how much changes, iterations, failures and achievements we have gone through. It all first began by experimenting with the Alvik with the idea that we would be able to use it to navigate autonomously around a room with a camera which could use object detection and feed that information to the robot. We had bold, ambitious ideas, but we lacked the experience needed to make that feasible. This reality came hard at us when we first played with the Arduino Alvik robot given to us. We were able to make it push pieces of paper off the table without the Alvik falling on the ground, but soon enough we encountered issues when the idea we had programmed the Alvik to do did not turn out the way we expected it to. The way <em>we</em> thought the robot would execute the code was not the way the robot <em>actually</em> ran it.  So, we had to simplify things. In the hunt for advice, we turned towards a Masters student at the University of Toronto, specializing in AI and robotics, who helped carve us a roadmap to completing our project. She helped us realize that we had to tackle our projects in smaller steps instead of tackling the entire project at once. This approach helped us break our project into multiple, more manageable pieces that could then later be combined together in our final product. </p>
<p>&nbsp;&nbsp;&nbsp;&nbsp;This is when we developed the idea for our final project, which would be a line following robot which could pick things up using a custom robotic arm. In terms of software, we programmed Alvik's functions using C++ in the Arduino IDE using functions from the Arduino Alvik library. For the colour detection of the ping pong balls, we used the OpenCV library and used Python to program colour detecting software, which ran on a Raspberry Pi serially connected to the Alvik. We also worked on the custom robotic arm with SOLIDWORKS, a computer-aided design software suite.</p>
<p>&nbsp;&nbsp;&nbsp;&nbsp;We encountered many problems when developing the functions of the robot. Initially, we had planned to place obstacles on our line following path to add an element of complexity to our project. This worked perfectly when we just implemented a feature where the Alvik would go around an object. However, when we combined this feature with the line following, it failed to deliver consistent results, which caused us to scrap this idea entirely. We tried adjusting the values at which the conditions were triggered, but we soon discovered using the Serial Monitor that the values the Alvik were producing were too inconsistent with our needs. It was quite annoying because we devoted time and effort to make it work, but we accepted that this was part of the process: some ideas need to be scrapped even if we did not like it. </p>
<p>&nbsp;&nbsp;&nbsp;&nbsp; In our challenge that we designed for the Alvik, we also wanted the Alvik to stop at a designated area to scan for the ping pong balls laid out around the track. We used the colour sensors of the Alvik to detect the yellow line at which it should stop at. We first thought that the Alvik would stop at the yellow line given the readings of the RGB values below the Alvik range in between certain values that we had recorded using the Serial Monitor. But, when we put it on the track, the Alvik either stopped randomly at certain places or skipped over the yellow line entirely: another example where my code worked in an unexpected way. We solved this by replacing yellow tape with the white board below, which saved us because the Alvik detected white much more consistently than yellow. This was an important milestone in our project, since all of our features for the Alvik were complete and we could finally come together to put all the pieces of our project together.</p>
<p>&nbsp;&nbsp;&nbsp;&nbsp; We came out of this project with a better understanding on what it takes to engineer an electronics project from scratch. We discovered a path for learning, while fine tuning my technical skills. We made ideas. We changed ideas. We scrapped ideas. We realized our ideas. It took lots of <em>trying</em> and <em>doing</em> to achieve meaningful results in my project, we are proud for the work we have achieved. In the future, we would like to implement a feature we did not have time to implement: object detection using artificial intelligence. Along with this, we would like to use this object detection to drive the Alvik around. We would also try different external ultrasonic sensors for object detection to improve on the accuracy of the distance calculations of the Alvik. This could then be implemented into the current project by reinstating the objects on the line following track.</p>

### References
<p>[1] AerospaceControlsLab. (2015, July 21). <em>Controlling Self Driving Cars.</em> [Video]. YouTube. <a href= "https://www.youtube.com/watch?v=4Y7zG48uHRo&ab_channel=AerospaceControlsLab">https://www.youtube.com/watch?v=4Y7zG48uHRo&ab_channel=AerospaceControlsLab</a>. Accessed 24 May 2025.</p>
<p>[2] Arduino Education. (n.d.). <em>Courses</em>. Arduino. <a href = "https://www.arduino.cc/education/courses">https://www.arduino.cc/education/courses</a>. Accessed 24 May 2025.  </p>
<p>[3] Cavagnolo, P. (2024, September 30). <em>Arduino Alvik API Overview</em>. Arduino Docs. <a href = "https://docs.arduino.cc/tutorials/alvik/api-overview/">https://docs.arduino.cc/tutorials/alvik/api-overview/</a>. Accessed 24 May 2025.</p>
<p>[4] freedomwebtech. (2022, April 5). <em>colortracking</em> [GitHub Repository]. GitHub. <a href = "https://github.com/freedomwebtech/colortracking">https://github.com/freedomwebtech/colortracking</a>. Accessed 24 May 2025.</p>
<p>[5] Pronest IoT. (2024, August 5). <em>Communication Between ESP32 and Raspberry Pi Using UART</em>. Medium. <a href = "https://protonestiot.medium.com/communication-between-esp32-and-raspberry-pi-using-uart-7b776786c08a">https://protonestiot.medium.com/communication-between-esp32-and-raspberry-pi-using-uart-7b776786c08a</a>. Accessed 24 May 2025.</p>
<p>[6] Rosebrock, A. (2021, July 8). <em>Find distance from camera to object/marker using Python and OpenCV</em>. pyimagesearch. <a href = "https://pyimagesearch.com/2015/01/19/find-distance-camera-objectmarker-using-python-opencv/">https://pyimagesearch.com/2015/01/19/find-distance-camera-objectmarker-using-python-opencv/</a>. Accessed 24 May 2025.</p>

<p>[7] Tech With Tim. (2019, June 13). <em>How to Take Photos and Videos with Raspberry Pi Camera Module</em> [Video]. YouTube. <a href = "https://www.youtube.com/watch?v=nx8gDSS1vO4&ab_channel=TechWithTim">https://www.youtube.com/watch?v=nx8gDSS1vO4&ab_channel=TechWithTim</a>. Accessed 24 May 2025.</p>
<p>[8] zoomkat. (2012, April). You can capture the values as a string, and then convert the string into a number. The below shows how [Comment on the online forum post <em>Read line from Serial</em>]. Arduino Forum. <a href = "https://forum.arduino.cc/t/read-line-from-serial/98251/5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">https://forum.arduino.cc/t/read-line-from-serial/98251/5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</a>. Accessed 24 May 2025.</p>

### Acknowledgements
<p>I would like to give a big thank you to my teammate, Semih Eski, who took time and effort to dedicate on working on our project. I would also like to thank Professor Joel Trudeau and his paracurricular organization, SPACE, for the opportunity he gave me to learn how to develop a project from scratch.</p>

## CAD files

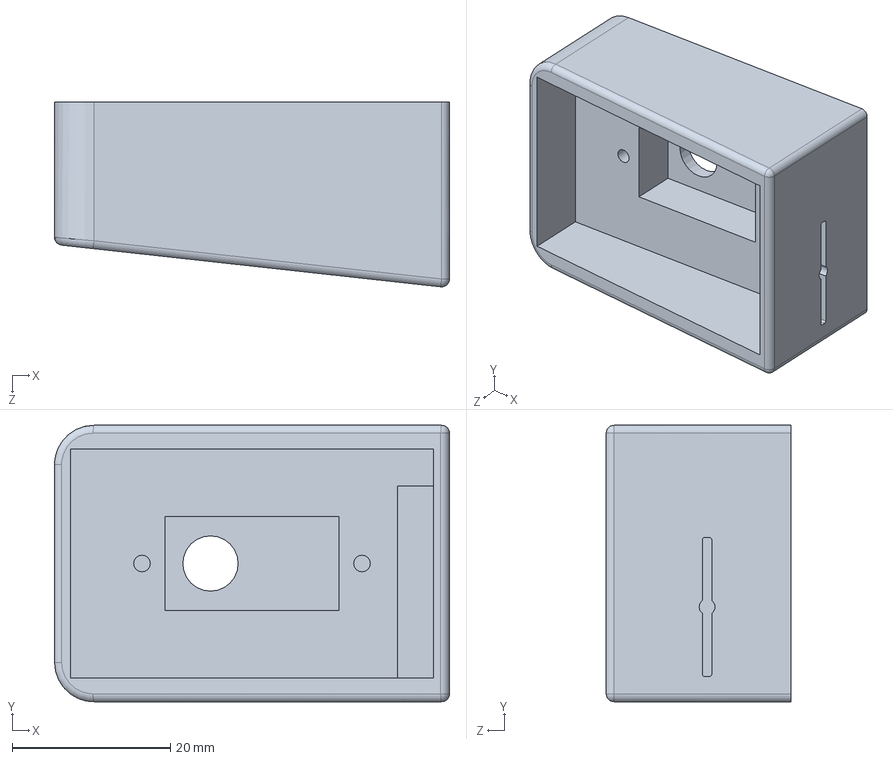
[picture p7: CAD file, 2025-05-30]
robot_arm_parts/Hand.SLDPRT
50.0 x 35.0 x 23.4 mm

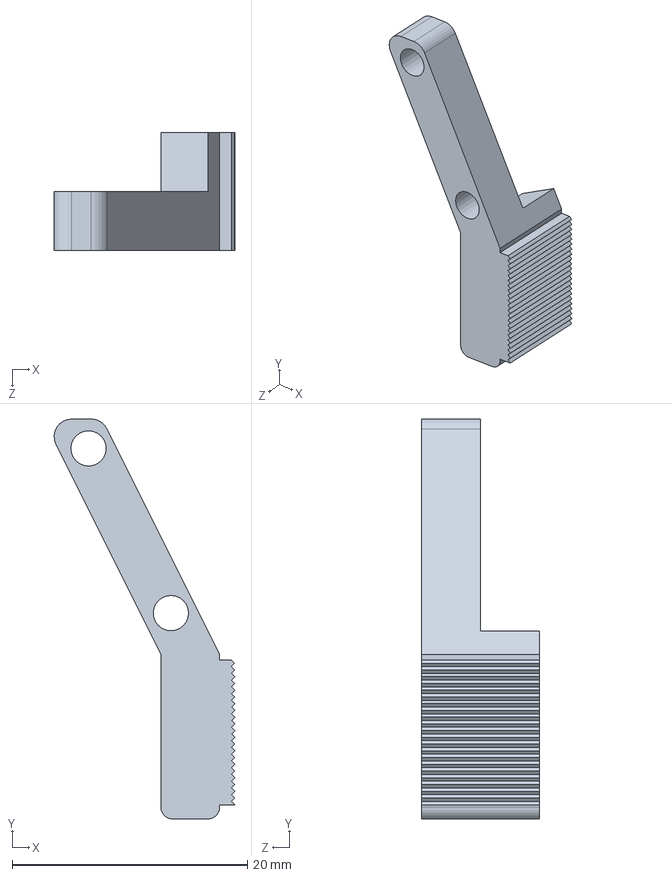
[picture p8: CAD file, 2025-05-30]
robot_arm_parts/Gripper1.SLDPRT
15.4 x 34.0 x 10.0 mm

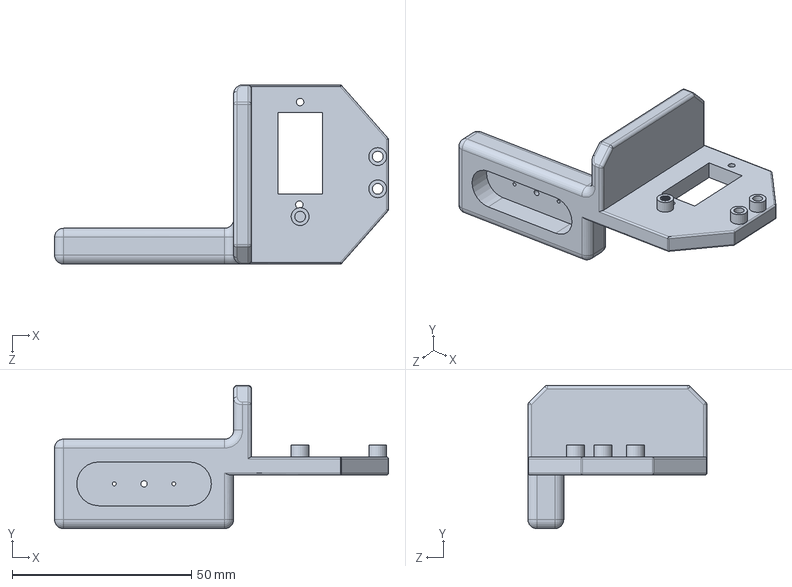
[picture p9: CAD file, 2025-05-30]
robot_arm_parts/GripperBase.SLDPRT
93.2 x 40.0 x 50.0 mm

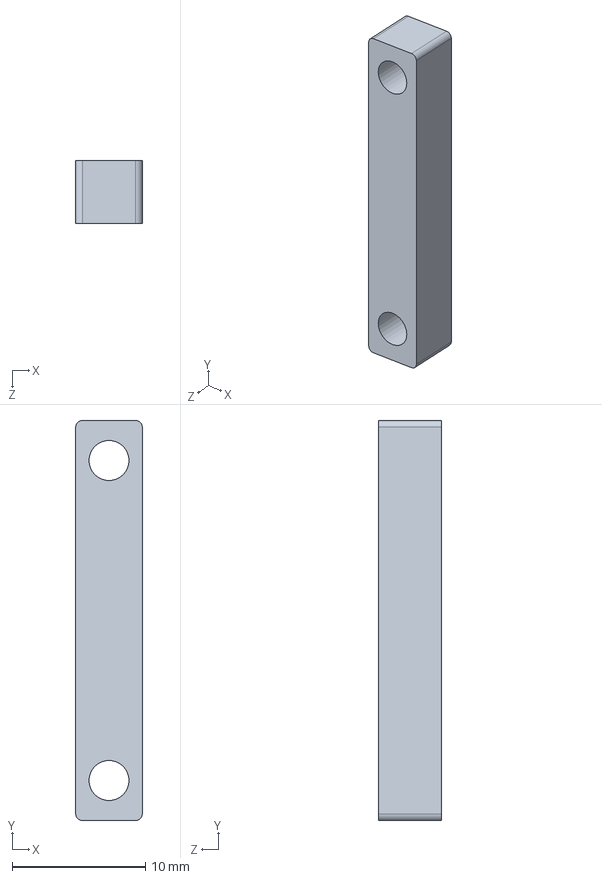
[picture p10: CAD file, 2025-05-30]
robot_arm_parts/GripperSupport1.SLDPRT
5.00 x 30.0 x 4.70 mm

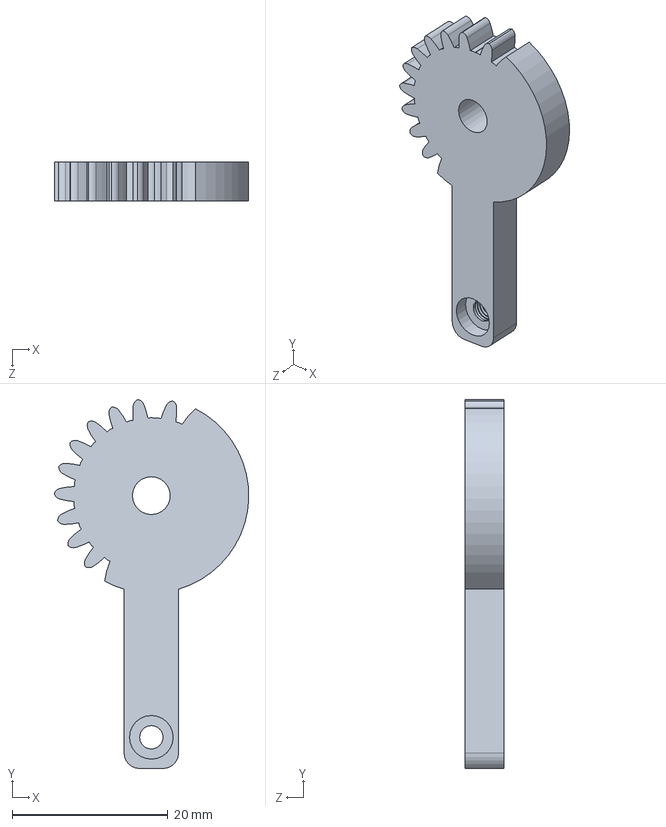
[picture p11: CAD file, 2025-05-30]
robot_arm_parts/GearGripper.SLDPRT
24.9 x 47.3 x 5.00 mm

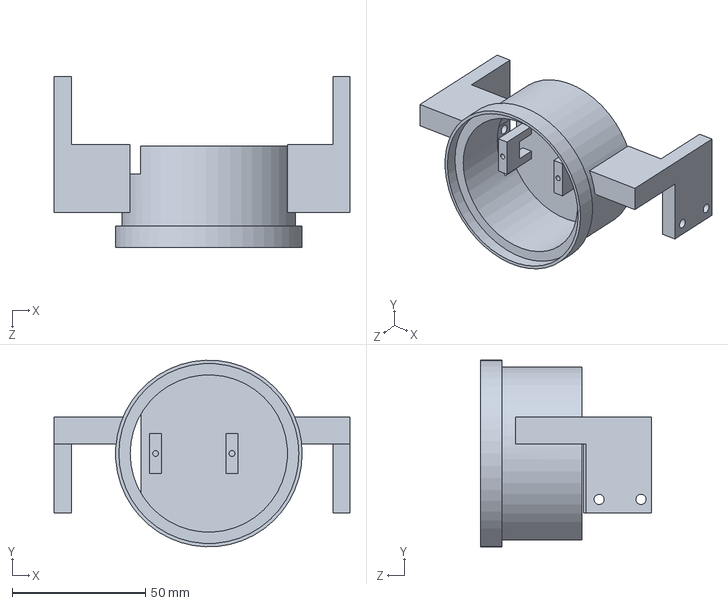
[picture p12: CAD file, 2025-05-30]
robot_arm_parts/armsupport1.SLDPRT
111.0 x 70.0 x 64.0 mm

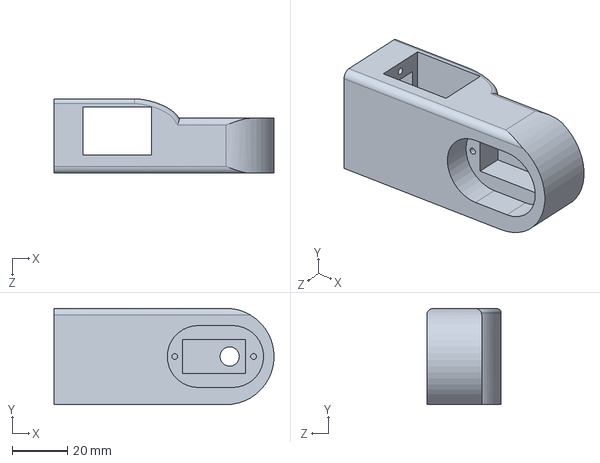
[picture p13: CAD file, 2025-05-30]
robot_arm_parts/Forearm.SLDPRT
80.0 x 35.0 x 27.1 mm

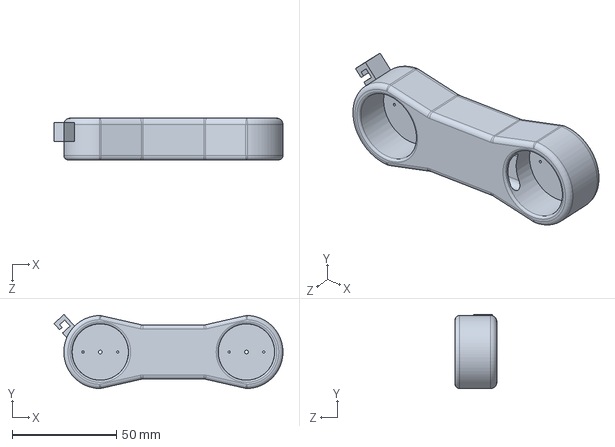
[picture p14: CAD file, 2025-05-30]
robot_arm_parts/Arm.SLDPRT
109.7 x 35.5 x 20.0 mm

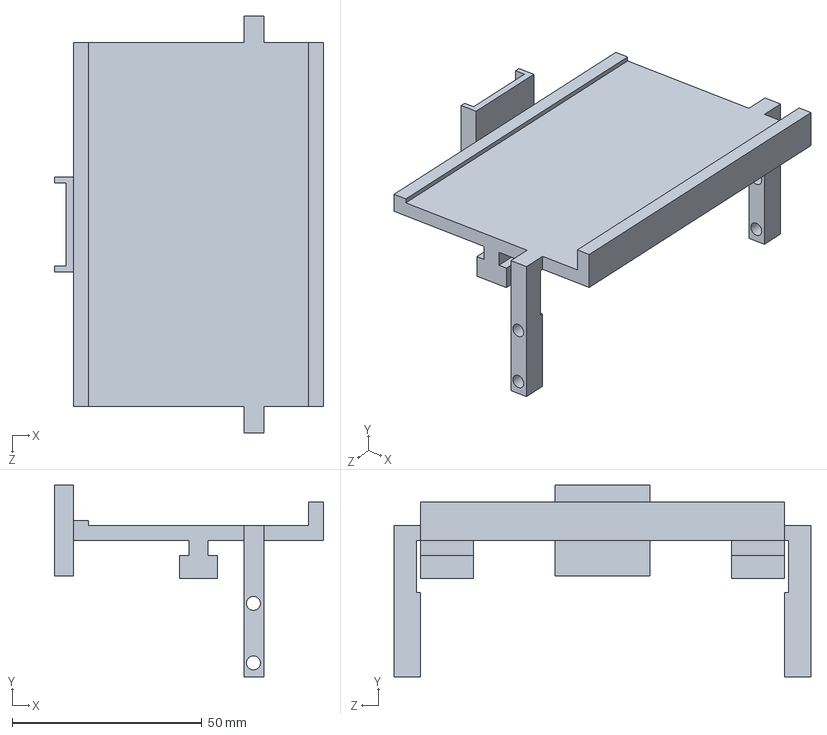
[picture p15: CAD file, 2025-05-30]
robot_arm_parts/rasppiholder.SLDPRT
71.0 x 50.6 x 110.0 mm

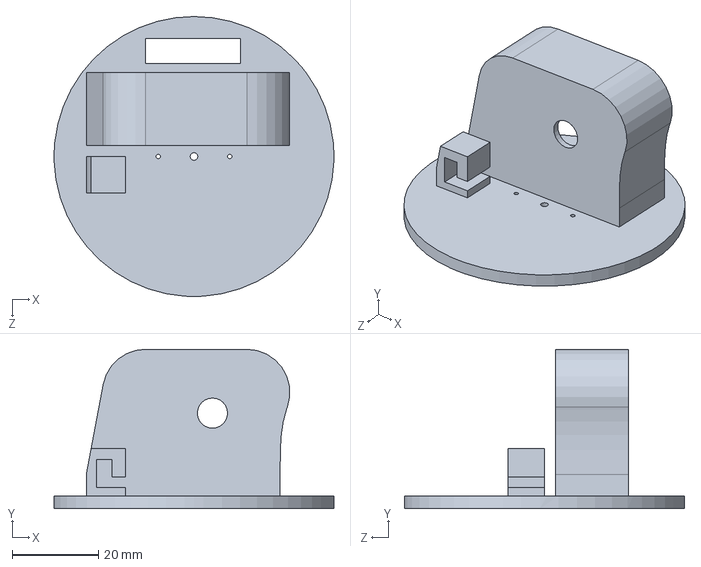
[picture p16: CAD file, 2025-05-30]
robot_arm_parts/Base.SLDPRT
65.0 x 37.0 x 65.0 mm

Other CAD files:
robot_arm_parts/Gripper2.SLDPRT
robot_arm_parts/GearGripperLEFT.SLDPRT

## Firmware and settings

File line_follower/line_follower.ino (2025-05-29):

// Include the necessary packages
#include "Arduino_Alvik.h"

// Instanstiate the alvik object
Arduino_Alvik alvik;

// Variables for line following
int line_sensors[3];
float error = 0;
float control = 0;
float kp = 50.0;
// List containing colors of RGB
int rgb_colors[3];
// String read from Serial communication from Raspberry Pi
String readString;

// Setting Alvik up for Serial communication
void setup() {
  Serial.begin(115200); // Establish Serial port communication via USB-C
  while(!Serial){
    ; // wait for USB serial to come out
  }
  alvik.begin();
  alvik.left_led.set_color(0,0,1);
  alvik.right_led.set_color(0,0,1);

  while(!alvik.get_touch_ok()){
    delay(50);
  }
}


void loop() {
  while (!alvik.get_touch_cancel()){
    
    // Turns light below Alvik off (otherwise, blows the colour values)
    alvik.set_illuminator(false);

    // Retrives the IR sensor values and stores them in line_sensors list
    alvik.get_line_sensors(line_sensors[0], line_sensors[1], line_sensors[2]);
    alvik.get_color_raw(rgb_colors[0],rgb_colors[1],rgb_colors[2]); // returns RGB values into the list rgb_colors

    // Error for the line following is calculated
    error = calculate_center(line_sensors[0], line_sensors[1], line_sensors[2]);
    control = error * kp;

    // For Serial Monitoring of the colours below the Alvik
    Serial.print(rgb_colors[0]);
    Serial.print("\t");
    Serial.print(rgb_colors[1]);
    Serial.print("\t");
    Serial.print(rgb_colors[2]);
    Serial.print("\n");

    if ((rgb_colors[0] == 4) && (rgb_colors[1] == 4) && (rgb_colors[2] == 4 || rgb_colors[2] == 3)){ // If the triple (R,G,B) is any of these values, strong indication that yellow is below the Alvik
      alvik.left_led.set_color(1,0,0); // brake lights
      alvik.right_led.set_color(1,0,0);
      alvik.brake();
      delay(2000);
      alvik.rotate(14);
      delay(2000);
      alvik.set_wheels_speed(10,10);
      delay(2000);
      alvik.brake();
      delay(3000);
      
      // Alvik communicates via Serial to the Pi to take a photo and calculate the distance of the ping pong ball (if any)
      Serial.println("photo");
      
      // Alvik remains stopped while the Serial bus is empty
      while(Serial.available() <= 0){
        alvik.brake();
      }

      // Alvik reads from Serial if Pi is sending information over and reads the encoded message
      while(Serial.available()){
        if (Serial.available() > 0 ){
          char c = Serial.read();
          readString += c;
        }
      }

      int distance = readString.toInt(); // mm
      int rpm = 10; // rpm
      int time = 60000*distance/(rpm*3.14159*3.4); // milliseconds
      Serial.println(time); // prints the time needed in milliseconds in Serial Monitor
      alvik.set_wheels_speed(rpm,rpm); // Wheel speed set for Alvik to approach object
      delay(time); // Delays the exact time needed to travel the distance required
      alvik.brake(); // Alvik stops for 3 seconds to show it has ended this operation
      delay(3000);
    }

    // Deviation to the right
    else if (control > 0.2){
      alvik.left_led.set_color(1,0,0);
      alvik.right_led.set_color(0,0,0);
    }
    else{
      // Deviation to the left
      if (control < -0.2){
        alvik.left_led.set_color(0,0,0);
        alvik.right_led.set_color(1,0,0);
      }
      // On course
      else{
        alvik.left_led.set_color(0,1,0);
        alvik.right_led.set_color(0,1,0);
      }
    }
    
    // Speed adjusted so that the Alvik follows the line
    alvik.set_wheels_speed(30-control, 30+control);
    delay(100);
  }
  
  while (!alvik.get_touch_ok()){
    alvik.left_led.set_color(0,0,1);
    alvik.right_led.set_color(0,0,1);
    alvik.brake();
    delay(100);
  }
}

// Calculates the center of the IR sensors
float calculate_center(const int left, const int center, const int right){
  float centroid = 0.0; 
  float sum_weight = left + center + right;
  float sum_values = left + center * 2 + right * 3;
  if (sum_weight!=0.0){                                                         // divide by zero protection
    centroid=sum_values/sum_weight;
    centroid=-centroid+2.0;                                                     // so it is right on robot axis Y
  }
  return centroid;
}

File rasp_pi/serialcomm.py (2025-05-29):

# Import the necessary packages
import serial
import time
from picamera import PiCamera
import time
import math
from imutils import paths
import numpy as np
import imutils
import cv2
import os


KERNEL = np.ones((5, 5), np.uint8)

# You must insert the lower and upper bounds for the colours you wish to detect. Note lighting conditions greatly affect the success rate of this.
ORANGE_LOWER = np.array([4, 140, 58])  # HSV Values
ORANGE_UPPER = np.array([12, 214, 129])  # HSV Values

# Pi establishes serial communication with the Alvik
ser = serial.Serial('/dev/ttyACM0', 115200, timeout=1)
time.sleep(2)

# Initialize the camera object for taking picture of the ball
camera = PiCamera()

# Function that identifies and returns the position and radius of the object of the colour you're trying to detect


def find_marker(image):

    # Declares colour spectrum
    hsv = cv2.cvtColor(image, cv2.COLOR_BGR2HSV)

    # Mask of the object
    mask = cv2.inRange(hsv, ORANGE_LOWER, ORANGE_UPPER)
    mask = cv2.morphologyEx(mask, cv2.MORPH_OPEN, KERNEL, iterations=1)
    mask = cv2.morphologyEx(mask, cv2.MORPH_CLOSE, KERNEL, iterations=1)

    # Finds countours of the object with the colour
    cnts = cv2.findContours(mask, cv2.RETR_EXTERNAL, cv2.CHAIN_APPROX_SIMPLE)
    cnts = imutils.grab_contours(cnts)

    # If no contour is detected around object
    if not cnts:
        return None

    c = max(cnts, key=cv2.contourArea)
    # Minimizes the risk of detecting dots with that colour (ensures the entire ping pong ball is enclosed, not just specific dots with the specific colour)
    if cv2.contourArea(c) < 200:
        return None

    # Position as well as the radius of the object is returned
    (x, y), radius = cv2.minEnclosingCircle(c)
    return (x, y), radius

# Function that calculates the distance of the object to the camera


def distance_to_camera(knownWidth_cm, focalLength_px, perWidth_px):
    return (knownWidth_cm * focalLength_px) / perWidth_px


# To calibrate the calculations, you must measure beforehand the distance of the object from the camera and its width
KNOWN_DISTANCE_CM = 18.25
KNOWN_WIDTH_CM = 4

# Path where the photo of the calibration photo is taken (You must take a new one every time with snap_photo.py if you go into a new environment)
calib_path = "/directory1/directory2/calibration_photo.jpg"

# If no calibration photo is found, a FileNotFoundError is raised
if not os.path.isfile(calib_path):
    raise FileNotFoundError(f"calibration image missing")

# The calibration image is read provided there is a path towards an existing one
calib_image = cv2.imread(calib_path)

# Finds the position as well as the radius of the object
res = find_marker(calib_image)

# If no marker is found, raises an error
if res is None:
    raise RuntimeError("No ball found")

# Variables for the camera
(center0, radius0) = res
perWidth0 = 2 * radius0
focalLength_px = (perWidth0 * KNOWN_DISTANCE_CM) / KNOWN_WIDTH_CM

# The Pi continues to read from the USB port for its signal to take a photo
while True:
    # Pi reads the messages in the Serial bus
    line = ser.readline().decode('utf-8').strip()

    # If the message is photo, then it captures a photo of the ball in front of it (if there is one)
    if line == "photo":
        time.sleep(2)

        # Photo is stored in a directory on your PC of your choosing
        camera.capture(
            "/directory1/directory2/folder_with_images/distance.jpg")

        # Checks the photos and identifies the ball in the image (if there is one)
        for imagePath in sorted(paths.list_images("/directory1/directory2/folder_with_images")):

            # Reads the image and determines if the colour is found by marking the object
            image = cv2.imread(imagePath)
            res = find_marker(image)

        # If no ball is detected, the message serially communicated to Alvik is 0 meters (i.e. no ball is in front of it)
        if res is None:
            dist_cm = 0
            print("No ball found.")
            message = f"{str(math.floor(dist_cm))}"
            encoded_message = message.encode()
            ser.write(encoded_message)

        # Otherwise, a ball is detected and it calculates the distance in front of it
        else:
            (x, y), radius = res
            perWidth = 2 * radius
            dist_cm = distance_to_camera(
                KNOWN_WIDTH_CM, focalLength_px, perWidth)
            message = f"{str(math.floor(dist_cm))
                         }"
            encoded_message = message.encode()
            ser.write(encoded_message)
        time.sleep(5)
        break

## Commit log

2025-05-14 Add brake lights to color detect func.
2025-05-21 Add files from Raspberry Pi
2025-05-22 Add Raspberry Pi files via upload
2025-05-23 Fix comment in Arduino + syntax highlighting
2025-05-29 Add comments in snap_photo.py
    [snap_photo.py]
2025-05-29 Add comment to snap_photo.py
    [snap_photo.py]
2025-05-29 Fix spacing and add comments in snap_photo.py
    [snap_photo.py]
2025-05-30 Add robotic arm parts SOLIDWORKS via upload
    [Arm.SLDPRT, Base.SLDPRT, Forearm.SLDPRT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]
2025-05-30 Update README.md
    done with wiring instructions
2025-07-29 solidworks assembly video
